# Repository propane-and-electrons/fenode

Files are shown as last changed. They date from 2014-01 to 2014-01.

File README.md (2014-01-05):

fenode
------
Flame effect control node: an Arduino compatible, 4 channel DC + 1 channel AC solid state relay with RS-485 communication and flame sensor built-in. Originally designed for and used by Super Street Fire.

4 DC channels and 1 AC channel makes this board very versatile. Use it to control flame effects with a hot surface igniter, or RGBW LEDs using the DMX512 protocol.

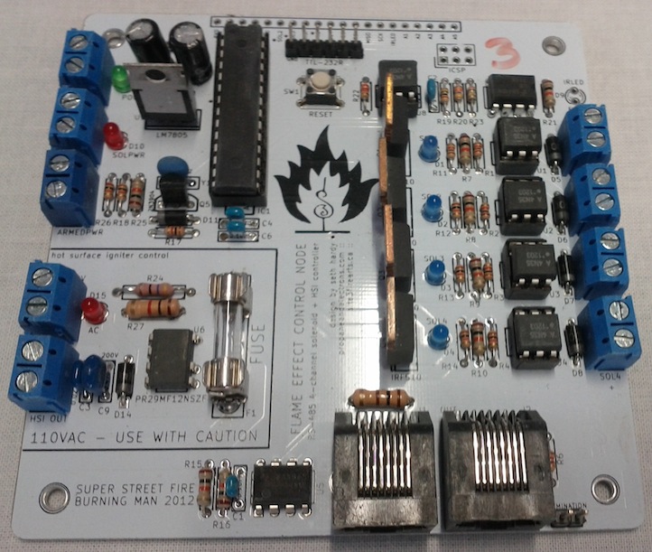
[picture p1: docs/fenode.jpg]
fenode photo


### Feature Summary

* Arduino compatible
* Programmable via 6-pin FTDI header or 6-pin ICSP header
* Four DC load channels switched via MOSFET
* One AC load channel switched via SSR
* Power connectors use 5mm screw terminals or Anderson Powerpole connectors
* Standard 5mm fuse for protection on AC channel
* RS-485 support (DMX512 compatible) via 8P8C connectors
* Termination resistor and jumper for serial connection
* All ATMega I/O pins are broken out on the board
* DC load power is optoisolated from the control system power
* Power connectors use 5mm screw terminals or Anderson Powerpole connectors
* Load power status is reported to the microcontroller via an optoisolated input pin
* Each output channel has a status LED for easy debugging
* IR LED connector for use as a flame sensor

### Documents

* [Schematic](docs/fenode-schematic.pdf)
* [Bill of Materials](docs/fenode-BOM.csv)

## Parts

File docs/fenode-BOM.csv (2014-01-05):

Designator | Part | Digikey ID | Quantity
C1, C4, C6, C8 | 0.1uF | 490-5369-ND | 4
C2 | 1nF | 490-3815-ND | 1
C3 | 0.022uF 630V | 445-2642-ND | 1
C5, C7 | 47uF | P13464-ND | 2
C9 | 0.47uF 200V | 490-4819-ND | 1
D1, D2, D3, D4, D10, D13, D15 | 3mm LED | 754-1606-ND | 7
D9 | IR LED | 751-1203-ND | 1
D5, D6, D7, D8, D11, D12, D14 | 1N4004 | 641-1311-1-ND | 7
F1 | 5mm fuse | F2460-ND | 1
XF1 | 5mm fuse holder | F4189-ND | 2
IC1 | ATMEGA328P | ATMEGA328P-PU-ND | 1
J1, J2 | 8P8C | 609-1046-ND | 2
JP1, XD9 | 2 pin header | A34253-40-ND | 4
P1, P2, P3, P4, P5, P6, P7, P8, P9 | 5mm screw terminal | ED2600-ND | 9
P10 | 2x3 pin header | A34344-40-ND | 3
P14 | 6 pin header | A34253-40-ND | 6
Q1, Q2, Q3, Q4 | IRF510 | IRF510PBF-ND | 4
Q5 | 2N3904 | 2N3904FS-ND | 1
R1, R2, R3, R4, R11, R12, R13, R14, R17, R18, R26 | 1k | 1.0KQBK-ND | 11
R5 | 100 1/2W | 100H-ND | 1
R6 | 120R | 120QBK-ND | 1
R7, R8, R9, R10, R15, R16, R21, R25 | 10k | 10KQBK-ND | 8
R19 | 1M | CF14JT1M00CT-ND | 1
R20 | 47k | 47QBK-ND | 1
R22 | 2.2k | 2.2QBK-ND | 1
R23 | 300k | 300QBK-ND | 1
R24 | 47 1W | 47WCT-ND | 1
R27 | 1k 1/2W | 1.0KH-ND | 1
SW1 | push button | SW400-ND | 1
U1, U2, U3, U4, U8 | 4N35 | 516-1557-5-ND | 5
XU1, XU2, XU3, XU4, XU8 | 6-DIP holder | A100203-ND | 5
U5 | MAX485 | 296-1739-5-ND | 1
U6 | S108T02 | 425-2396-5-ND | 1
U7 | LM358N | LM358NFS-ND | 1
U9 | LM7805 | LM7805CT-ND | 1
Y1 | 16MHz | 490-1214-ND | 1

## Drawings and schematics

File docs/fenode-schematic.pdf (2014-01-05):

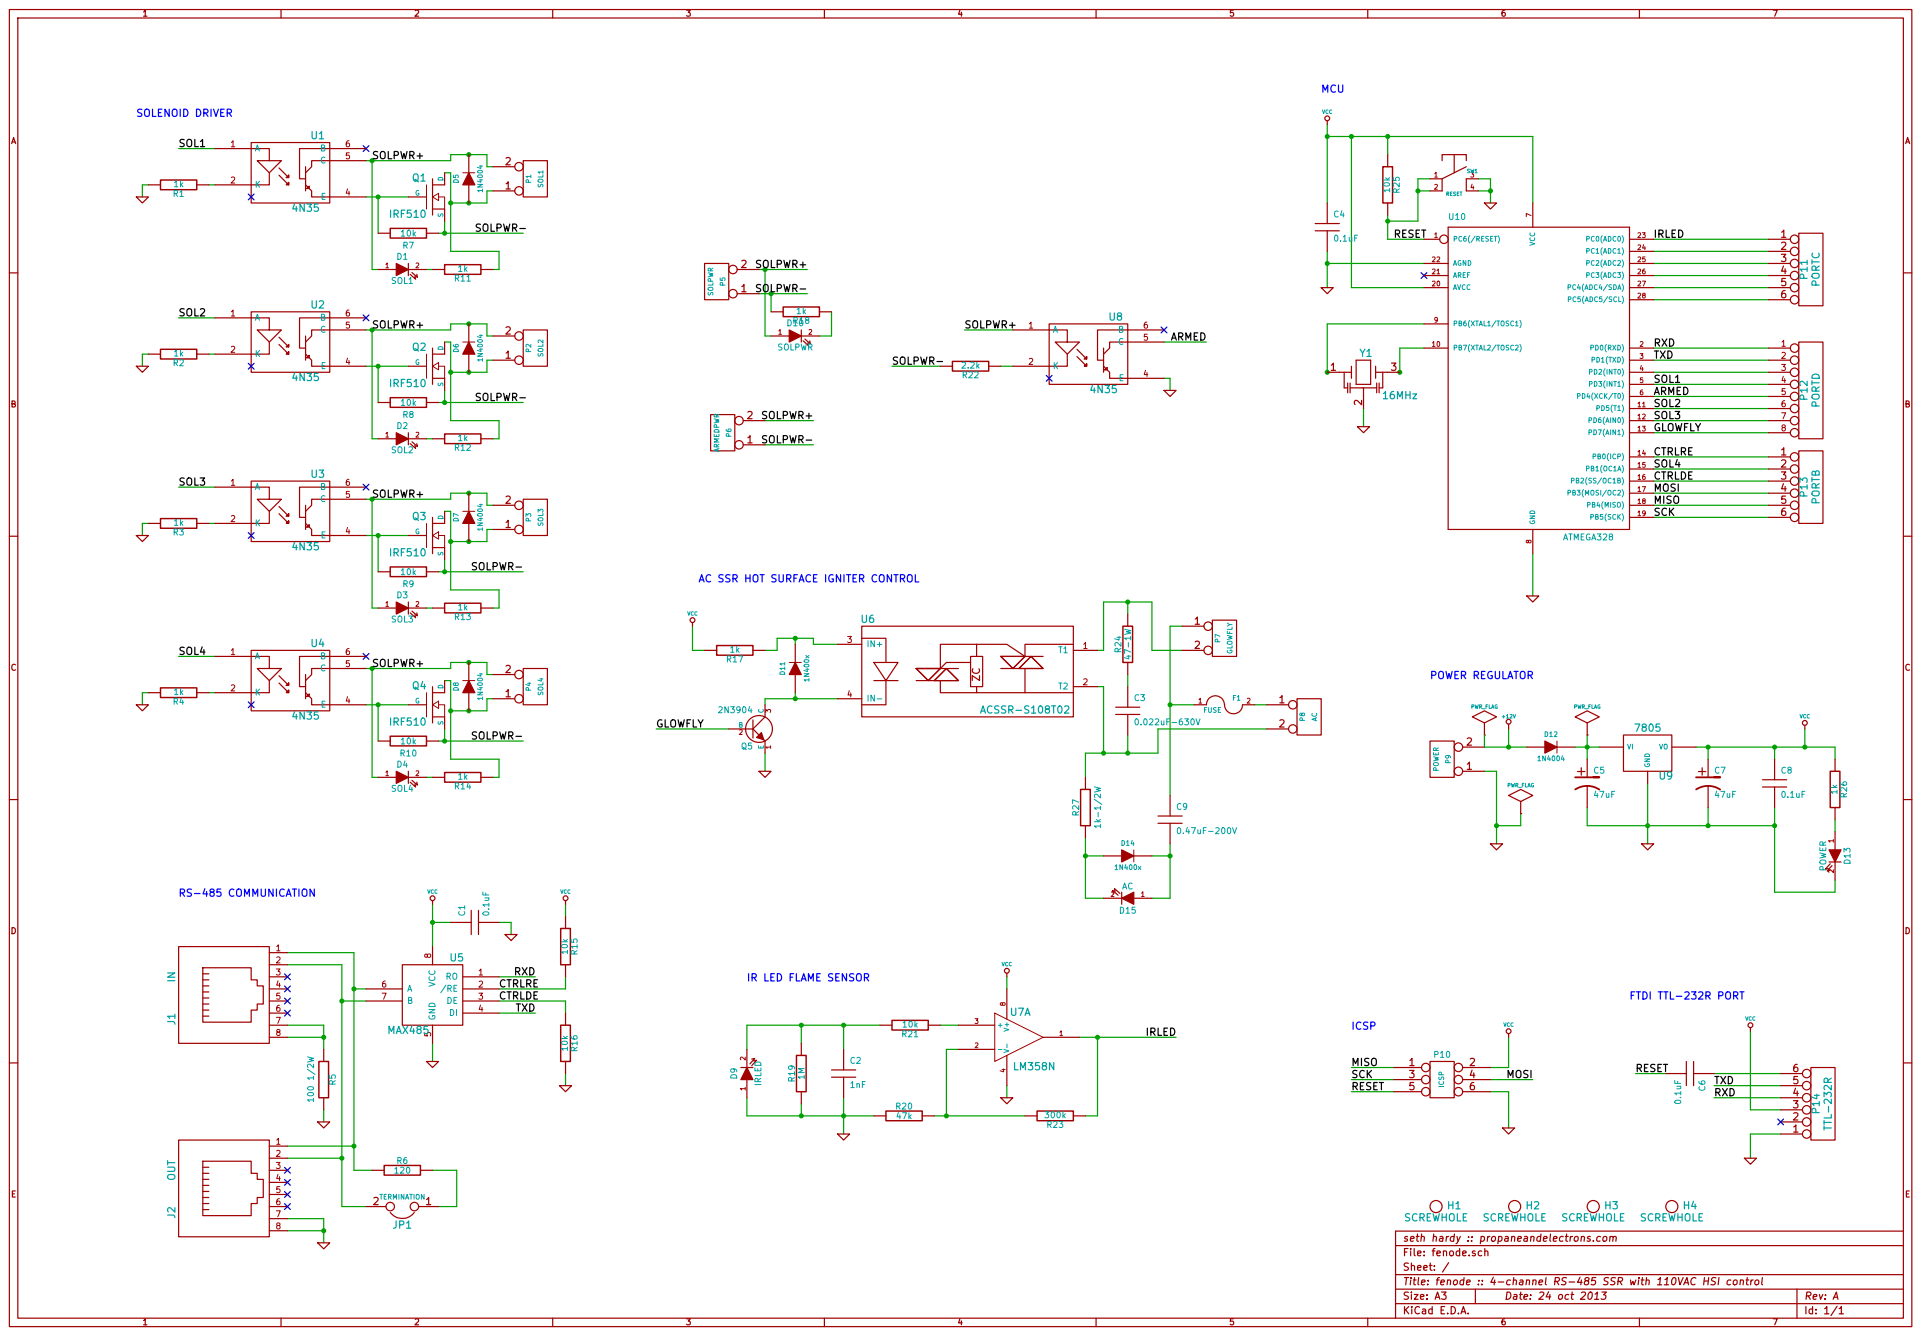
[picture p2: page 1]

1k AC SSR HOT SURFACE IGNITER CONTROL

IR LED FLAME SENSOR

H4 SCREWHOLE H3 SCREWHOLE H2 SCREWHOLE H1 SCREWHOLE

seth hardy :: propaneandelectrons.com
Title: fenode :: 4-channel RS-485 SSR with 110VAC HSI control File: fenode.sch Sheet: /

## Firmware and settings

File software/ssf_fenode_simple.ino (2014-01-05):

#define SOL1 3
#define SOL2 5
#define SOL3 6
#define SOL4 9
#define ARMED 4
#define HSI 7
#define DE 10
#define RE 8
#define IRLED 14

#define NODE 5
#define BROADCAST 0xFF
#define FRAME 0xAA

#define MAXSIZE 0x0B

// DEBUG 1 = debug serial output w/USB cable; DEBUG 0 = serial output over RS-485
#define DEBUG 0


void setup() {
  
  pinMode(SOL1, OUTPUT);
  digitalWrite(SOL1, LOW);
  pinMode(SOL2, OUTPUT);
  digitalWrite(SOL2, LOW);
  pinMode(SOL3, OUTPUT);
  digitalWrite(SOL3, LOW);
  pinMode(SOL4, OUTPUT);
  digitalWrite(SOL4, LOW);
  pinMode(HSI, OUTPUT);
  digitalWrite(HSI, LOW);
  pinMode(RE, OUTPUT); // RE receive active low
  if( DEBUG ) {
    digitalWrite(RE, HIGH);
  }
  else {
    digitalWrite(RE, LOW);
  }
  pinMode(DE, OUTPUT); // DE transmit active high
  digitalWrite(DE, LOW);
  
  digitalWrite(ARMED, HIGH);

  Serial.begin(57600);
  
  if( DEBUG ) {
    Serial.println("starting");
  }

}

byte c;
byte param;
int csum;
byte length;
byte i;
byte cmd[MAXSIZE];

void loop() {
  
  if(Serial.available() > 0) {
    c = Serial.read(); // framing byte 1
    if(c == FRAME) {
      do {
      } while( Serial.available() <= 0 );
      c = Serial.read(); // framing byte 2
      if(c == FRAME) {
        do {
        } while( Serial.available() <= 0);
        length = Serial.read(); // length
        if( (length > 0) && (length <= MAXSIZE) ) {
          do {
          } while( Serial.available() < length);
          for(i=0;i<length;i++) {
            cmd[i] = Serial.read();
          }
          for(;i<MAXSIZE;i++) {
            cmd[i] = 0;
          }
          do {
          } while( Serial.available() <= 0);
          csum = Serial.read();
          if( (cmd[0] == NODE) || (cmd[0] == BROADCAST) ) {
            if( DEBUG ) {
              //Serial.println("listening to message for me");
            }
            i = 0;
            //Serial.print(" |");
            for(c=0;c<length;c++) {
              i += cmd[c];
              //Serial.print(" ");
              //Serial.print(cmd[c], HEX);
              //Serial.print(" ");
            }
            //Serial.print("| ");
            c = ~i;
            if( (c != csum) && DEBUG ) {
              Serial.print("bad checksum, received ");
              Serial.print(csum);
              Serial.print(" expected ");
              Serial.println(c);
            }
            if(c == csum) {
              if( DEBUG ) {
                Serial.println("checksum ok ");
              }
            
              c = 1;
              while(c < length) {
                switch(cmd[c]) {
                  case '1' : 
                    c += 1;
                    if( c < length ) {
                      if( cmd[c] == 0 ) {
                        digitalWrite(SOL1, LOW);
                        if( DEBUG ) { Serial.println("effect 1 off"); }
                      }
                      else {
                        digitalWrite(SOL1, HIGH);
                        if( DEBUG ) { Serial.println("effect 1 on"); }
                      }
                      c += 1;
                    }
                    break;
                  case '2' :
                    c += 1;
                    if( c < length ) {
                      if( cmd[c] == 0 ) {
                        digitalWrite(SOL2, LOW);
                        if( DEBUG ) { Serial.println("effect 2 off"); }
                      }
                      else {
                        digitalWrite(SOL2, HIGH);
                        if( DEBUG ) { Serial.println("effect 2 on"); }
                      }
                      c += 1;
                    }
                    break;
                  case '3' :
                    c += 1;
                    if( c < length ) {
                      if( cmd[c] == 0 ) {
                        digitalWrite(SOL3, LOW);
                        if( DEBUG ) { Serial.println("effect 3 off"); }
                      }
                      else {
                        digitalWrite(SOL3, HIGH);
                        if( DEBUG ) { Serial.println("effect 3 on"); }
                      }
                      c += 1;
                    }
                    break;
                case '4' : 
                  c += 1;
                    if( c < length ) {
                      if( cmd[c] == 0 ) {
                        digitalWrite(SOL4, LOW);
                        if( DEBUG ) { Serial.println("effect 4 off"); }
                      }
                      else {
                        digitalWrite(SOL4, HIGH);
                        if( DEBUG ) { Serial.println("effect 4 on"); }
                      }
                      c += 1;
                    }
                    break;
                case 'A' :
                  c += 1;
                  if( c < length ) {
                    if(cmd[c] == '1') {
                      digitalWrite(HSI, HIGH);
                      if( DEBUG ) { Serial.println("hsi on"); }
                    }
                    else {
                      digitalWrite(HSI, LOW);
                      if( DEBUG ) { Serial.println("hsi off"); }
                    }
                    c += 1;
                  }
                  break;
                case 'E' : 
                  c += 1;
                  digitalWrite(SOL1, LOW);
                  digitalWrite(SOL2, LOW);
                  digitalWrite(SOL3, LOW);
                  digitalWrite(SOL4, LOW);
                  digitalWrite(HSI, LOW);
                  if( DEBUG ) { Serial.println("emergency stop"); }
                  break;
                case '?' :
                  c += 1;
                  if( !DEBUG ) {
                    digitalWrite(DE, HIGH);
                    digitalWrite(RE, HIGH);
                  }
                  Serial.write(0xAA);
                  Serial.write(0xAA);
                  Serial.write(6);
                  Serial.write((byte)0);
                  Serial.write(NODE);
                  Serial.print('S');
                  csum = NODE + 0x53;
                  if(digitalRead(ARMED) == HIGH) { 
                    Serial.print('0');
                    csum += 0x30;
                  }
                  else {
                    Serial.print('1');
                    csum += 0x31;
                  }
                  Serial.print('F');
                  csum += 0x46;
                  Serial.write(0x3F);
                  csum += 0x3F;
                  csum = csum % 256;
                  c = ~csum;
                  Serial.write(c);
                  Serial.flush();
                  delay(5);
                  if( !DEBUG ) {
                    digitalWrite(DE, LOW);
                    digitalWrite(RE, LOW);
                  }
   
                }  
              }
            }
          }
        }
      }
    }
  }
}

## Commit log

2013-03-13 initial commit, updated after SSF to use a different AC SSR
    [fenode.brd, fenode.sch]
2013-03-13 right right, trying to keep consistent directories
    [fenode.brd, fenode.sch]
2013-03-22 changing rj45 jack to remove nonexistent shield, fixing button symbol
    [fenode.sch]
2013-10-22 reversed powerpole orientation, moved AC components around, rerouted
    [fenode.brd, fenode.sch]
2013-10-22 how did that hole lose its name
    [fenode.brd]
2013-10-24 wrong switch footprint in schematic
    [fenode.sch]
2014-01-05 adding documentation
    [fenode-BOM.csv]
